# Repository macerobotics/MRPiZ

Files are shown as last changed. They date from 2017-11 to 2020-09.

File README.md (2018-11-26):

# MRPiZ robot

MRPiZ is small Open Source mobile robot.

# Overview

The repository is organised as follows:

* Hardware: schematics of the board
* Software: Python, C, java API and examples
* doc: Documentation

# Generating the documentation

The documentation is made using the [Sphinx tool](http://www.sphinx-dox.org) and the read the doc theme:

    sudo apt install python3-sphinx
    sudo pip3 install sphinx_rtd_theme

To generate the documentation go to the doc/fr directory, then run:

> make html

The output is generated in the build/html dir, open the build/html/index.html
file with firefox.

# Licence

<br />This work is licensed under a <a rel="license" href="http://creativecommons.org/licenses/by-sa/4.0/">Creative Commons Attribution-ShareAlike 4.0 International License</a>.

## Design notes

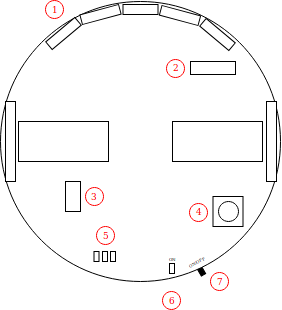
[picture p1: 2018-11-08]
doc/fr/source/overview/overview.png

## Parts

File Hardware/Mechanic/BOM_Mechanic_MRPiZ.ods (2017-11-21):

Description | Quantity | Part Number | Manufacturer
Pololu Ball Caster with 3/8″ Metal Ball | 1 | 951 | Pololu
Pololu Wheel 32×7mm Pair - White | 1 | 1088 | Pololu
Pololu Micro Metal Gearmotor Bracket Extended Pair | 1 | 1089 | Pololu

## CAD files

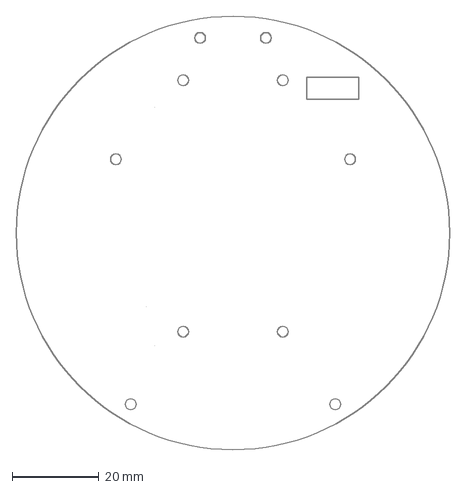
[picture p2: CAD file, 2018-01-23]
Hardware/Mechanic/Dessin_PlaqueMRPiZ.dxf
100.0 x 100.0 mm

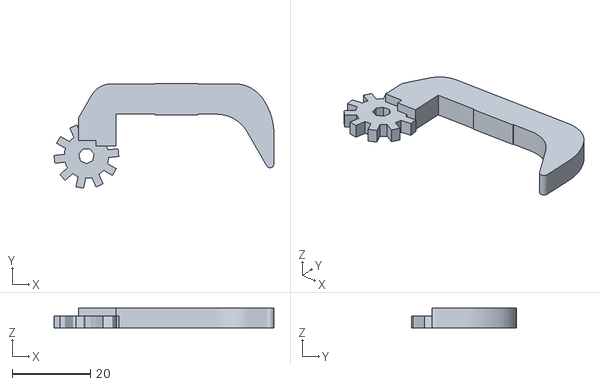
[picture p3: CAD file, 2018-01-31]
Hardware/Mechanic/Gripper/leftpincer.stl
56.3 x 26.8 x 5.00

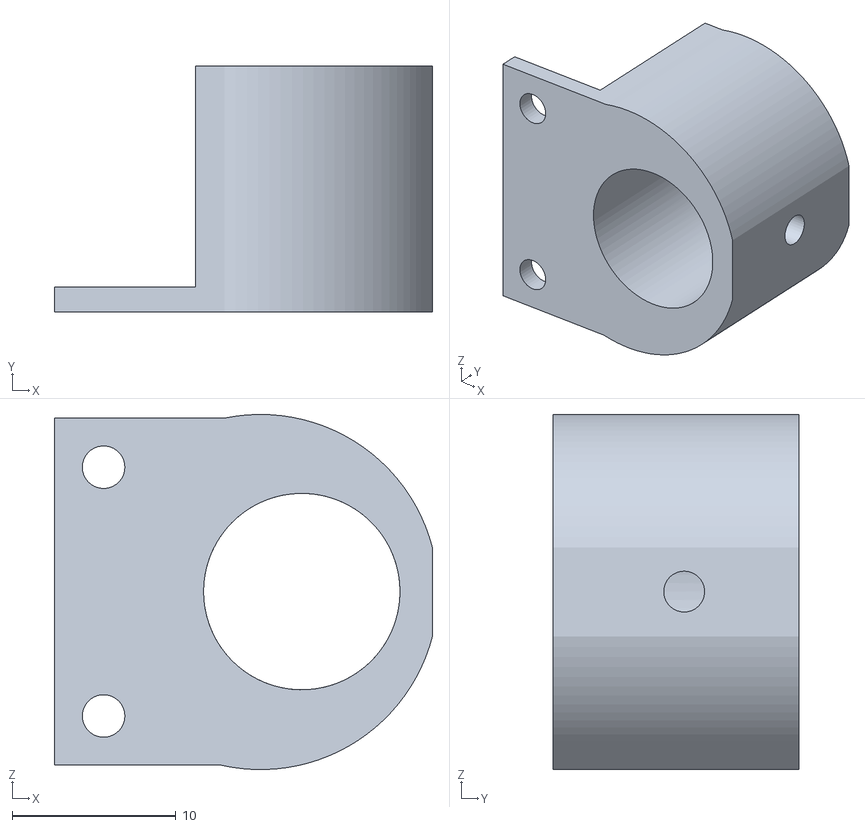
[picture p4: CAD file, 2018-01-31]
Hardware/Mechanic/PencilSupport/PencilSupport.stl
23.1 x 15.0 x 21.7

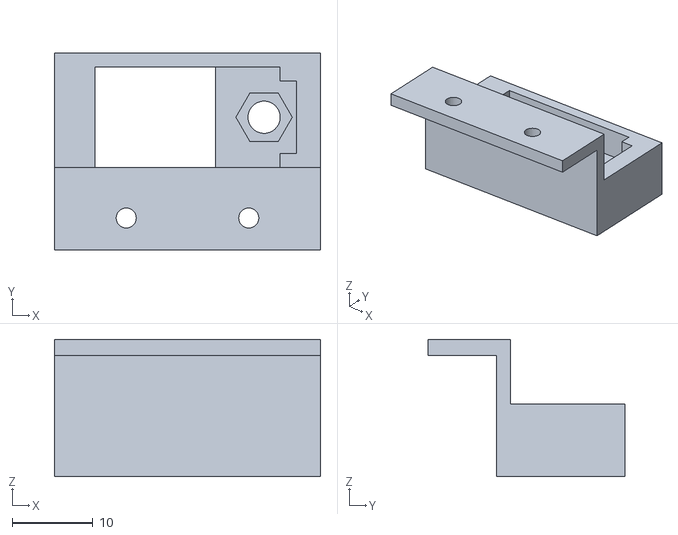
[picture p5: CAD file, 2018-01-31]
Hardware/Mechanic/Gripper/servobox.stl
33.0 x 24.5 x 17.0

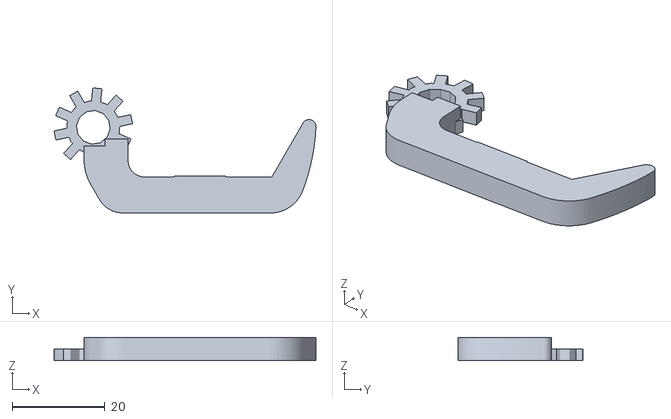
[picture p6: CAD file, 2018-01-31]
Hardware/Mechanic/Gripper/rightpincer.stl
56.5 x 27.0 x 5.00

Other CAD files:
Hardware/Mechanic/Gripper/leftpincer.f3d
Hardware/Mechanic/Gripper/rightpincer.f3d
Hardware/Mechanic/Gripper/servobox.f3d
Hardware/Mechanic/PencilSupport/PencilSupport.f3d

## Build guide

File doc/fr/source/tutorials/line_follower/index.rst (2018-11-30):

Suivi de ligne
==============

Ce tutorial présente l'implémentation d'un suivi de ligne pour le robot MRPiZ.

Matériel nécessaire
-------------------

* Un robot MRPiZ
* Une caméra compatible, idéalement grand angle, ce tutorial
  utilise une [caméra fisheye](https://www.kubii.fr/cameras-accessoires/2292-mini-camera-pour-pi-zero-fisheye-version-kubii-3272496012073.html).

.. warning:: Le connecteur de la raspberry pi zéro n'est pas le mmême que la raspberry pi normale. Il faut donc:

   * soit un adaptateur comme [celui-çi](https://www.kubii.fr/cables-cordons-raspberry-pi/1830-cable-pour-camera-pi-zero-edition-kubii-3272496006768.html),
   * soit une caméra compatible.

Logiciels nécessaire
--------------------

* Python 2.7 (déja installé par défaut),
* La bibliothèque Python MRPiZ (déja installée par défaut),
* OpenCV pour python:

```
$ sudo apt install python-opencv
```

Activation de video4linux
-------------------------

Deux méthodes sont possibles pour accèder à la caméra:

1. PiCamera: la méthode la plus répandue, mais lente car il est nécessaire de transformer l'image pour la mettre au bon format,
2. v4l: qui s'interface directement avec OpenCV, c'est la méthode choisie pour ce tutorial.

Il nous faut donc activer v4l:

.. code:: bash

   $ sudo modprobe bcm2835-v4l2

.. warning::

    Cette commande est a effectuer à chaque redémarrage.

Le suivi de ligne
-----------------

Le fichier complet se trouve dans `Software/Python/tutorials/line_follower/line.py`.

.. warning::

   Utilisez CTRL+C pour arrêter le robot.

Importation des modules
^^^^^^^^^^^^^^^^^^^^^^^

.. code-block:: python

   import numpy as np
   import cv2
   import sys
   from mrpiZ_lib import *

Parametres globaux
^^^^^^^^^^^^^^^^^^

.. code-block:: python

   # image size
   WIDTH = 640
   HEIGHT = 480

   # turn coeff
   COEFF = 0.05
   # base robot speed in straight line
   SPEED = 30

Activation de la caméra
^^^^^^^^^^^^^^^^^^^^^^^

Pour améliorer les performances, la résolution est réduite à 640 pixels en
largeur et 480 en hauteur.

.. code-block:: python

   video_capture = cv2.VideoCapture(0)
   video_capture.set(3, WIDTH)
   video_capture.set(4, HEIGHT)

Boucle principale
^^^^^^^^^^^^^^^^^

La boucle principale va fonctionner à l'infini, pour l'arrêter il faudra
appuyer sur CTRL+C.

.. code-block:: python

   try:
       while(True):

Capture de l'image
^^^^^^^^^^^^^^^^^^

Première étape, on commence par capturer une image.

.. code-block:: python

   # Capture the frames
   ret, frame = video_capture.read()

Voici un exemple d'image capturée:

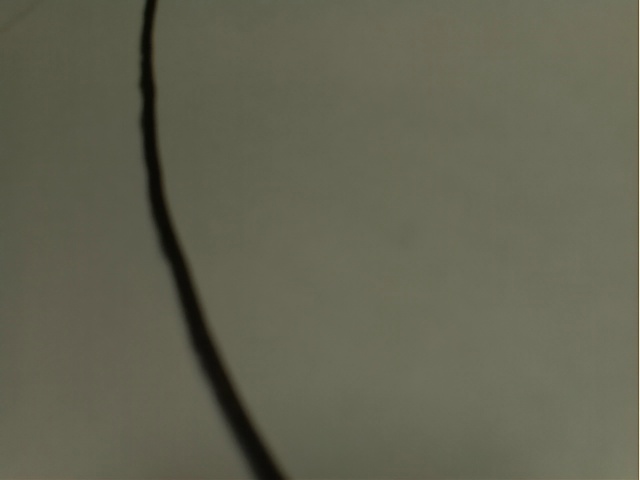
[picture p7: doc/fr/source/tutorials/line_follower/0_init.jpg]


Suppression de la partie haute
^^^^^^^^^^^^^^^^^^^^^^^^^^^^^^

Pour améliorer les performances, on ne va garder que la partie basse de l'image:

.. code-block:: python

   # Crop the image
   # Keep the 100 lower pixels
   crop_img = frame[379:480, 0:640]



Niveaux de gris
^^^^^^^^^^^^^^^

Ensuite on passe l'image en niveaux de gris:

.. code-block:: python

   # Convert to grayscale
   gray = cv2.cvtColor(crop_img, cv2.COLOR_BGR2GRAY)



Flou
^^^^

Un filtre afin de rendre flou les lignes de l'image est appliqué, il permet de
rendre plus efficace les étapes suivantes:

.. code-block:: python

   # Gaussian blur
   blur = cv2.GaussianBlur(gray,(5,5),0)



Seuillage
^^^^^^^^^

Ensuite on va filtrer les parties claires de l'image pour ne garder les parties
noires, pour cela, un filtre de seuillage est appliqué:

.. code-block:: python

   # Color thresholding
   ret,thresh = cv2.threshold(blur,60,255,cv2.THRESH_BINARY_INV)



Détection de contours
^^^^^^^^^^^^^^^^^^^^^

Ensuite, on va utiliser openCV pour détecter les contours:

.. code-block:: python

   # Find the contours of the frame
   contours,hierarchy = cv2.findContours(thresh.copy(), 1, cv2.CHAIN_APPROX_NONE)



Extraction du plus gros contour
^^^^^^^^^^^^^^^^^^^^^^^^^^^^^^^

Il nous faut ensuite extraire la ligne la plus large trouvée afin d'éliminer
les fausses détections:

.. code-block:: python

   # Find the biggest contour (if detected)
   if len(contours) > 0:
       c = max(contours, key=cv2.contourArea)
       M = cv2.moments(c)

       # Skip to avoid div by zero
       if int(M['m00']) == 0:
           continue

Calcul du milieu de la ligne
^^^^^^^^^^^^^^^^^^^^^^^^^^^^

Une fois les contours de la ligne détectée, on calcul le centre de la ligne,
c'est la que l'on veut que le robot aille:

.. code-block:: python

   # Get the line center
   cx = int(M['m10']/M['m00'])
   cy = int(M['m01']/M['m00'])

Contrôle des moteurs
^^^^^^^^^^^^^^^^^^^^

Une correction proportionnelle à la différence entre la position de la ligne et
le milieu de l'image est calculée.  Les moteurs sont ensuite commandés pour
ralentir un des moteurs et accélérer l'autre, ceci afin de faire tourner le
robot en direction du centre de la ligne.

.. code-block:: python

   delta = COEFF * (cx - 320)
   motorRight(0, SPEED - delta)
   motorLeft(0, SPEED + delta)

Clavier
^^^^^^^

Enfin, deux lignes de code permettent d'arrêter le robot quand on appuie sur
CTRL+C.

.. code-block:: python

   except KeyboardInterrupt:
       stop()

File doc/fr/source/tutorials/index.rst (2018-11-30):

=========
Tutorials
=========

.. toctree::
   :maxdepth: 2
   :caption: Contents:

   line_follower/index

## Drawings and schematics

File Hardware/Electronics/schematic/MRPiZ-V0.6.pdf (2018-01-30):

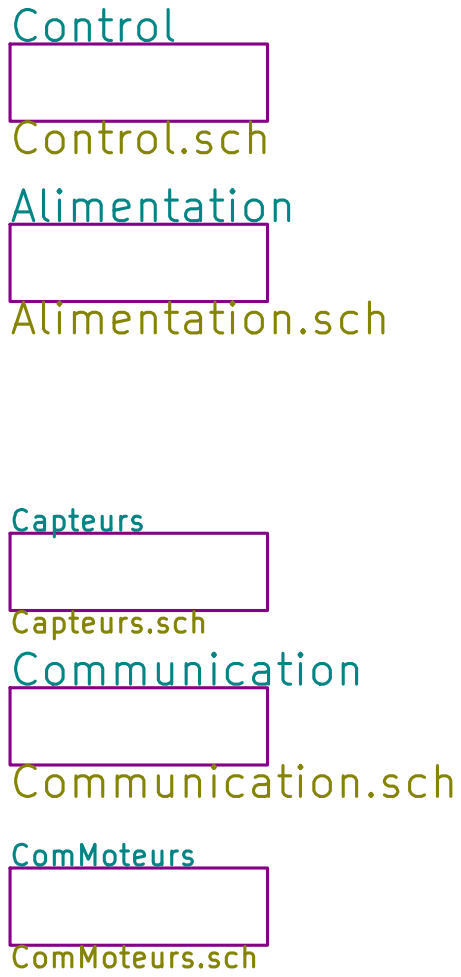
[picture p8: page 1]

ComMoteurs ComMoteurs.sch Control

Control.sch
File: carte_rants_V1.sch Sheet: / Alimentation Alimentation.sch

Capteurs Capteurs.sch Communication

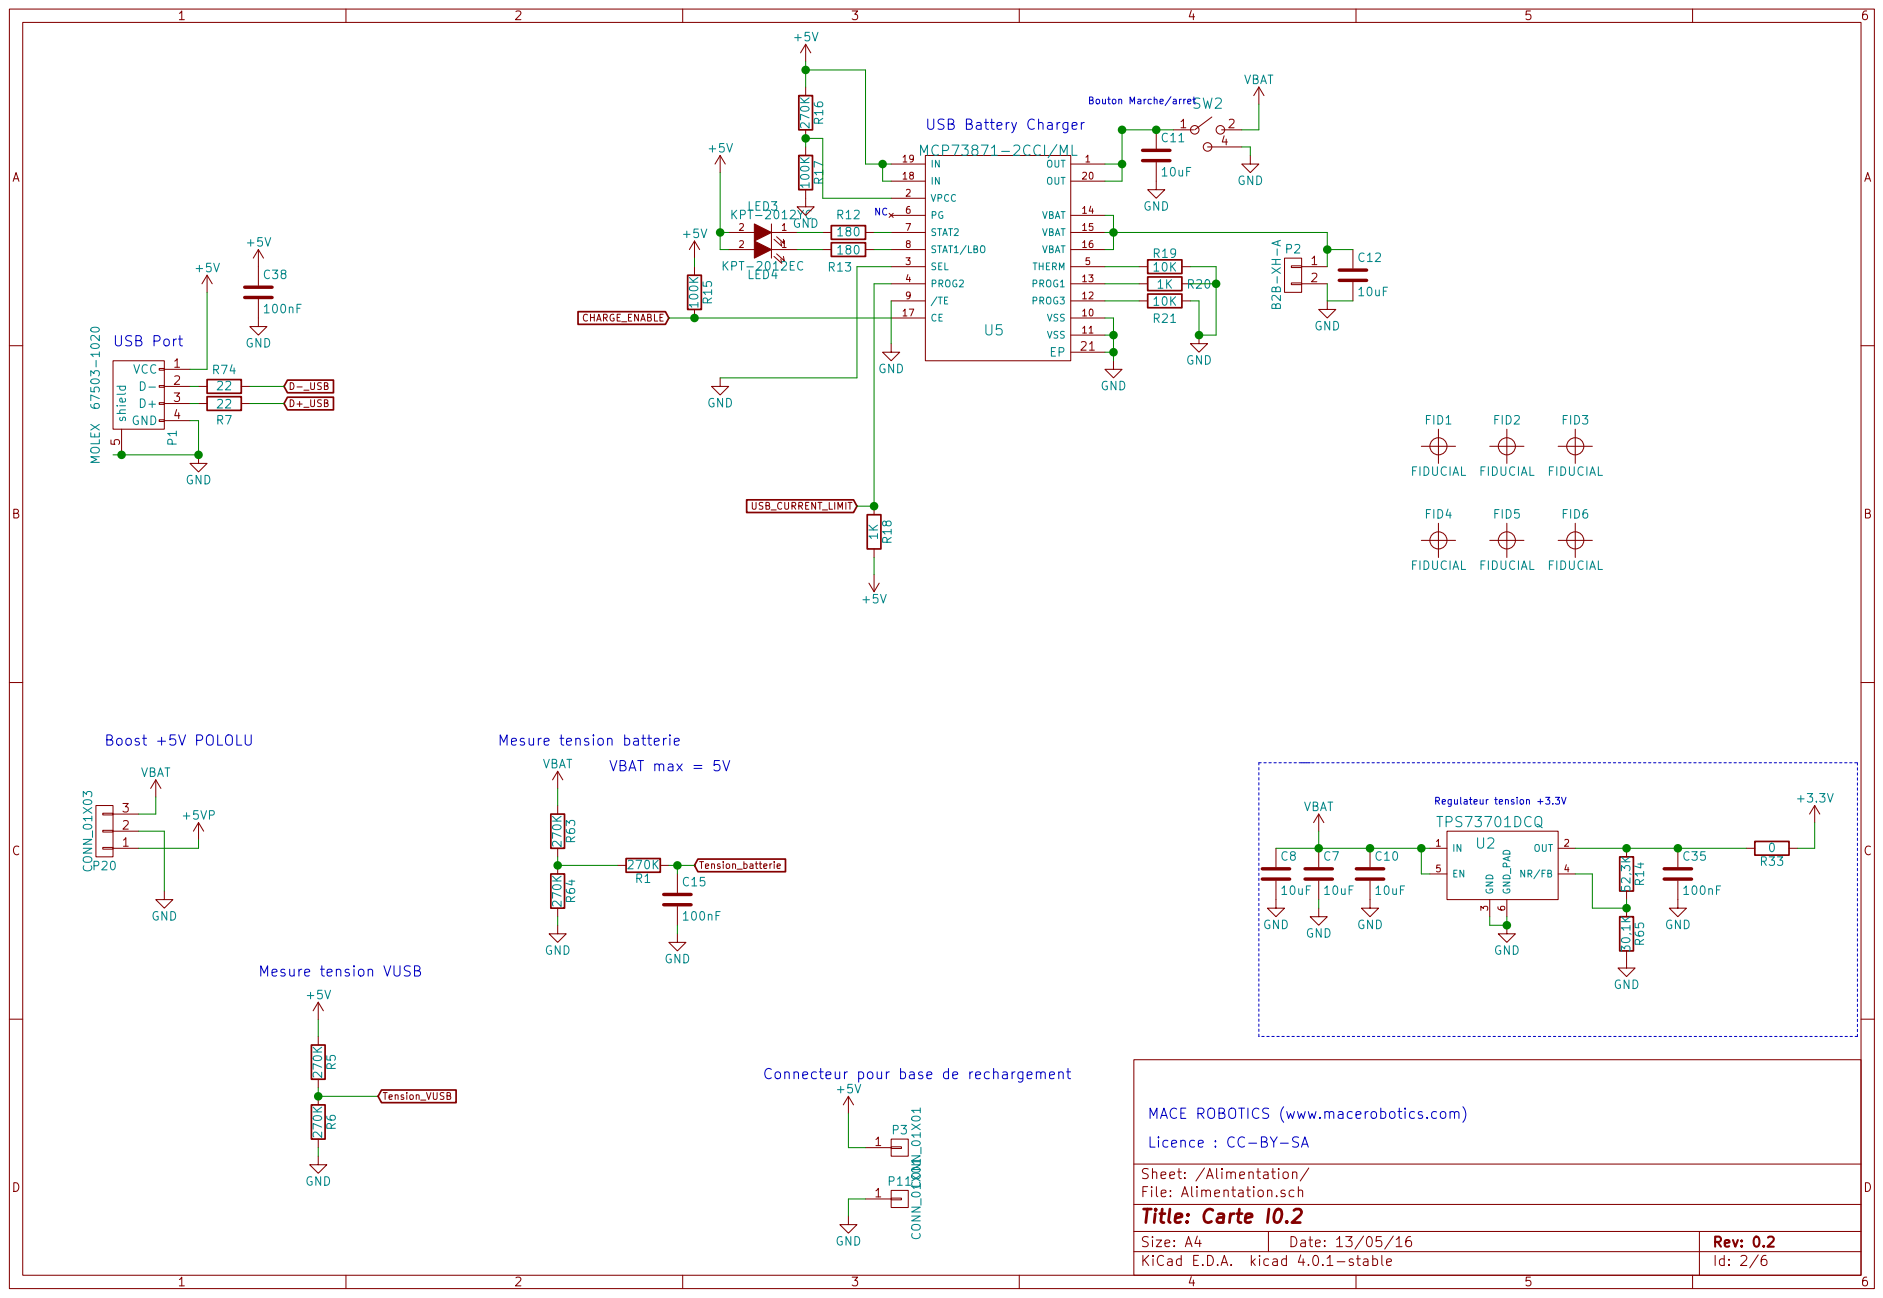
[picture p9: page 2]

VBAT 270K R63 270K R64 Mesure tension batterie GND

1 P11 GND Connecteur pour base de rechargement +5V

Licence : CC-BY-SA

File: Alimentation.sch Sheet: /Alimentation/
Id: 2/6 Title: Carte I0.2

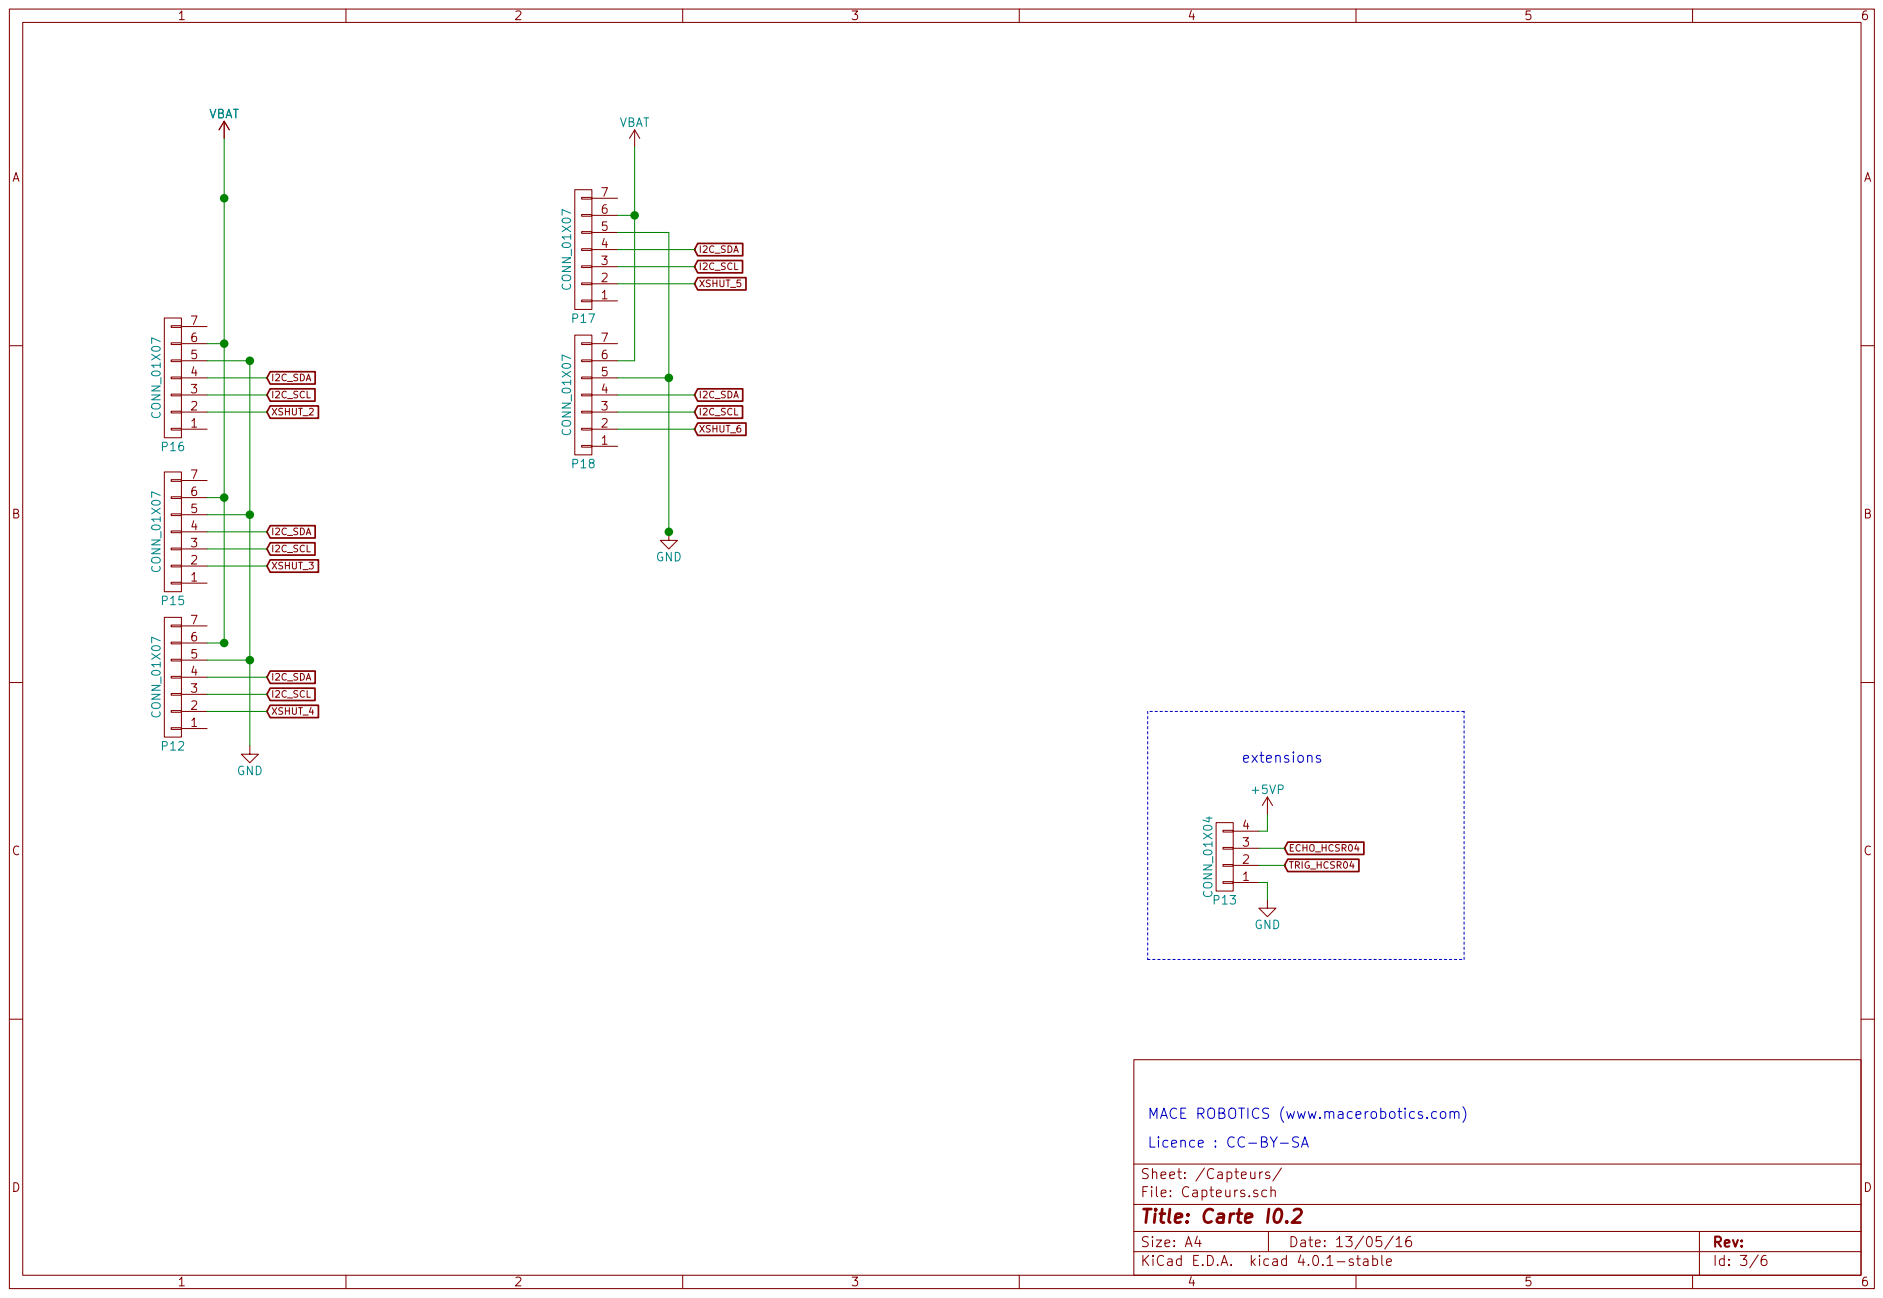
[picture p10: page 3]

MACE ROBOTICS (www.macerobotics.com)

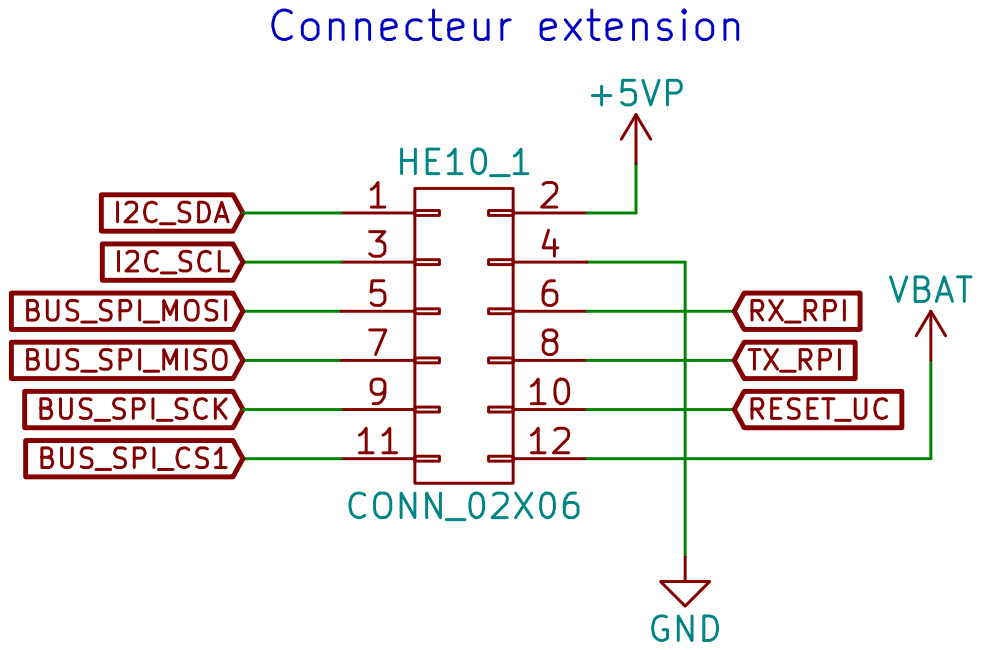
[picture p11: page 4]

Licence : CC-BY-SA

File: Communication.sch Sheet: /Communication/
Id: 4/6 Title: Carte I0.2

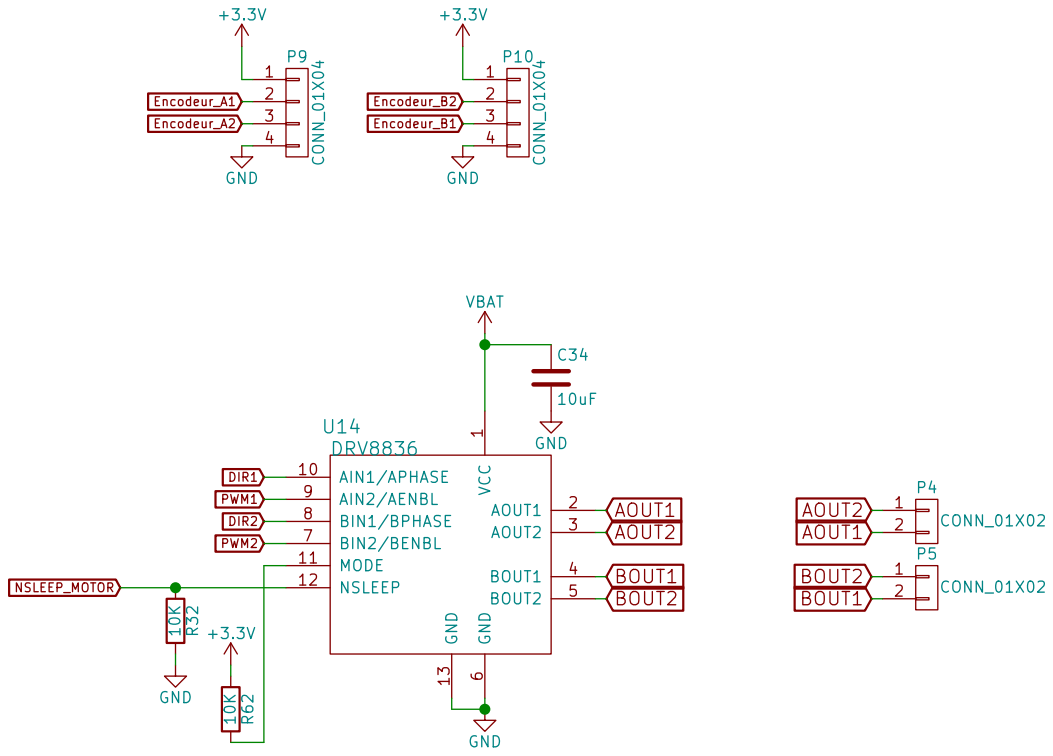
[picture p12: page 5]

4 P9 CONN_01X04 +3.3V
File: ComMoteurs.sch Sheet: /ComMoteurs/ VCC

6 BIN2/BENBL 7 BIN1/BPHASE 8 AIN2/AENBL 9 AIN1/APHASE 10 MODE 11 NSLEEP 12 GND 13 U14 DRV8836 GND

Licence : CC-BY-SA

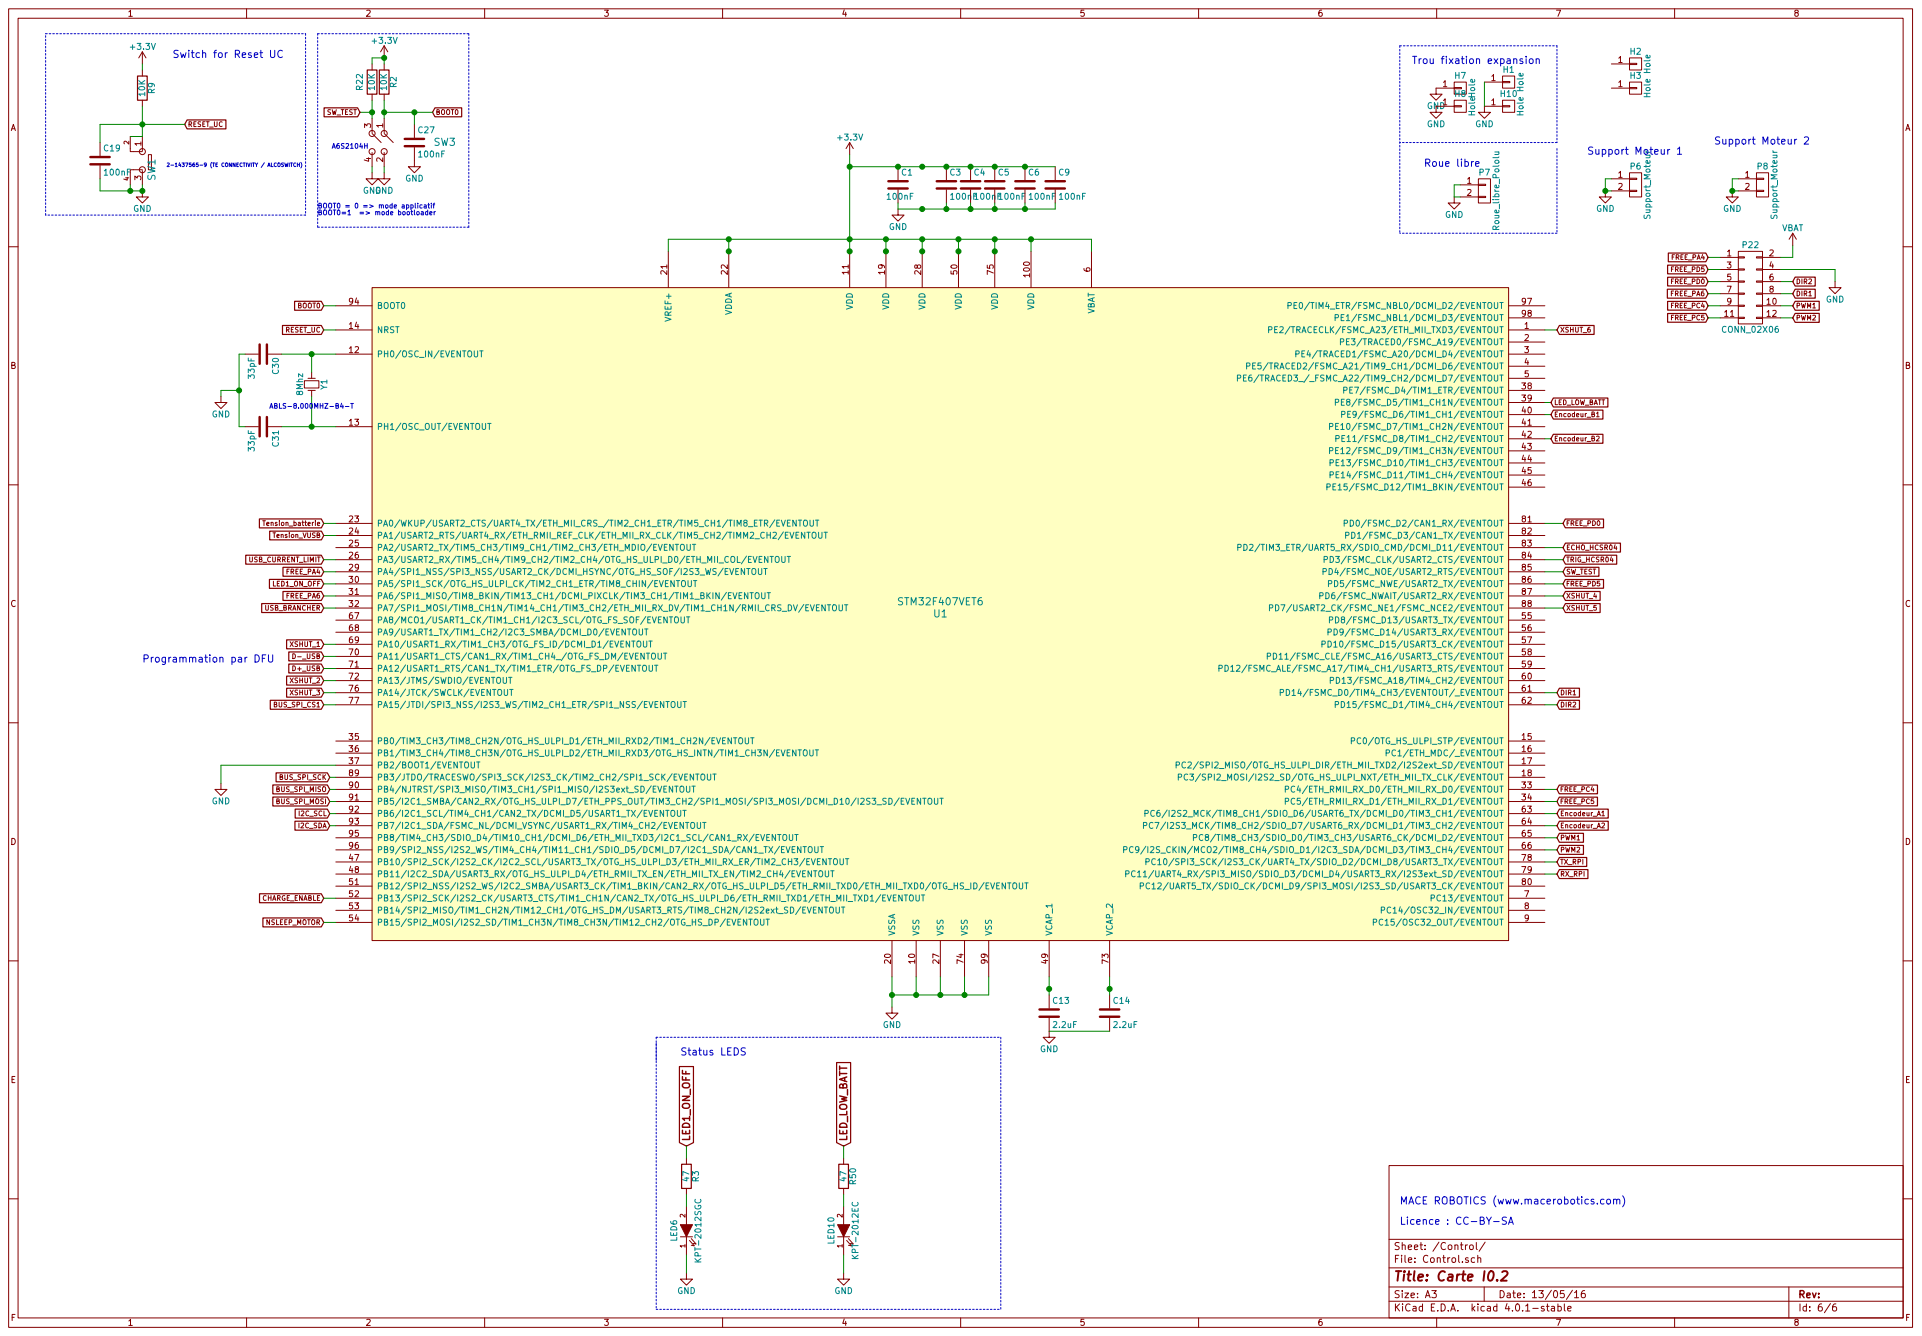
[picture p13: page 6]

BOOT0BOOT0 = 0 => mode applicatif BOOT0=1 => mode bootloader R2 10K
RESET_UC GND

2-1437565-9 (TE CONNECTIVITY / ALCOSWITCH) Switch for Reset UC

LED_LOW_BATT MACE ROBOTICS (www.macerobotics.com)

6 PC13/EVENTOUT 7 PC14/OSC32_IN/EVENTOUT 8 PC15/OSC32_OUT/EVENTOUT 9 VSS 10 VSSA 20

File: Control.sch Sheet: /Control/ GND

Licence : CC-BY-SA

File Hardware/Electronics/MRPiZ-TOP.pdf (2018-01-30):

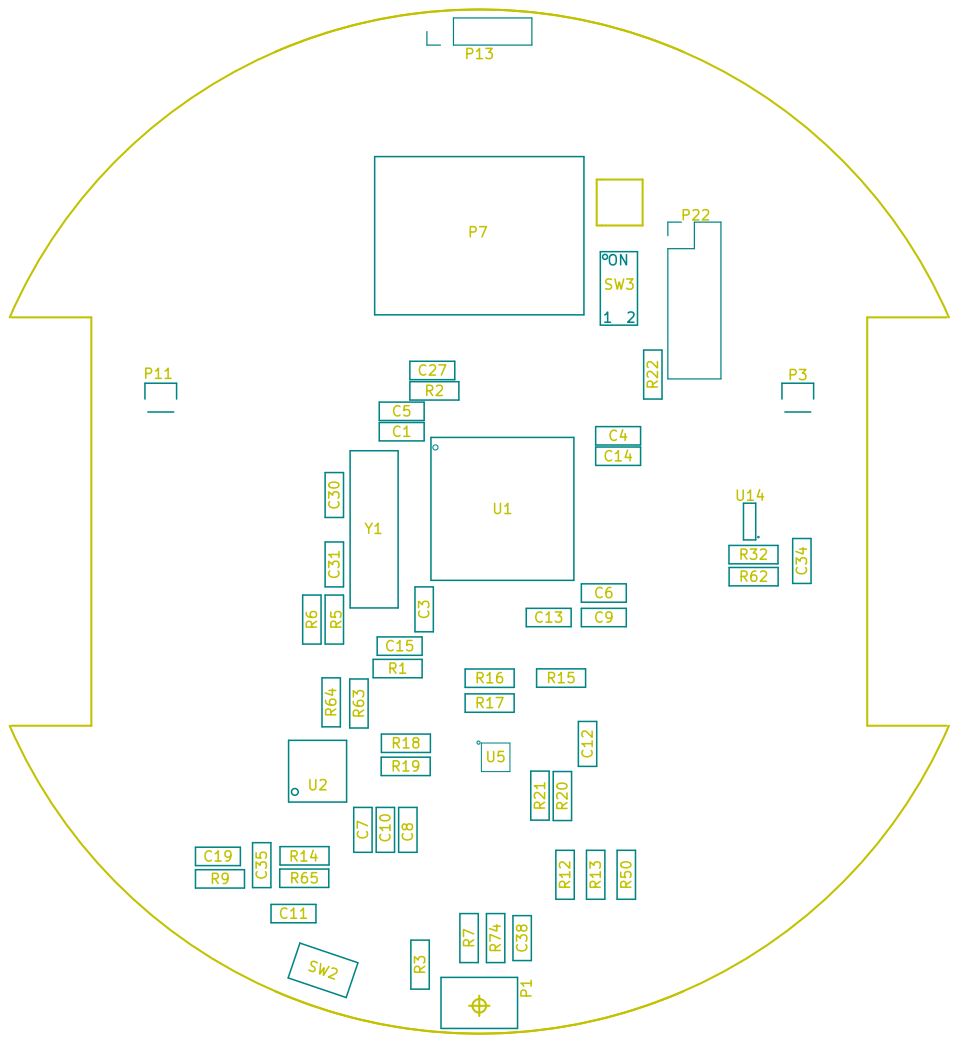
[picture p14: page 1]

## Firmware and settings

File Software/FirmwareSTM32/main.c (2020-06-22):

/**
  ******************************************************************************
  * @file    main.c
  * @author  Ac6
  * @version V1.0
  * @date    12/06/20
  * @brief   main function.
  ******************************************************************************
*/


#include "stm32f4xx.h"
#include "board.h"


/* Private function prototypes -----------------------------------------------*/
void SystemClock_Config(void);

int main(void)
{

  /* Reset of all peripherals, Initializes the Flash interface and the Systick. */
  HAL_Init();

  /* Configure the system clock */
  SystemClock_Config();

  // init delay functions
  Delay_init();

  // init scheduler
  schedulerInit();

  Board_init();

  // init serial communication between RPi and STM32
  ComRPI_init();

  RobotState_init();

  Motors_init();

  // init magnetic encoder
  encoder_init();

  Usart_Send_String(UART4, "START ROBOT MRPiZ");

  positionControl_init();

  ProxSensorsVL6180_init();


  while(1)
  {

	  schedulerManage();

  }// end while
}


/**
  * @brief System Clock Configuration
  * @retval None
  */
void SystemClock_Config(void)
{
  RCC_OscInitTypeDef RCC_OscInitStruct = {0};
  RCC_ClkInitTypeDef RCC_ClkInitStruct = {0};

  /** Configure the main internal regulator output voltage
  */
  __HAL_RCC_PWR_CLK_ENABLE();
  __HAL_PWR_VOLTAGESCALING_CONFIG(PWR_REGULATOR_VOLTAGE_SCALE1);
  /** Initializes the CPU, AHB and APB busses clocks
  */
  RCC_OscInitStruct.OscillatorType = RCC_OSCILLATORTYPE_HSI;
  RCC_OscInitStruct.HSIState = RCC_HSI_ON;
  RCC_OscInitStruct.HSICalibrationValue = RCC_HSICALIBRATION_DEFAULT;
  RCC_OscInitStruct.PLL.PLLState = RCC_PLL_ON;
  RCC_OscInitStruct.PLL.PLLSource = RCC_PLLSOURCE_HSI;
  RCC_OscInitStruct.PLL.PLLM = 8;
  RCC_OscInitStruct.PLL.PLLN = 168;
  RCC_OscInitStruct.PLL.PLLP = RCC_PLLP_DIV2;
  RCC_OscInitStruct.PLL.PLLQ = 4;
  if (HAL_RCC_OscConfig(&RCC_OscInitStruct) != HAL_OK)
  {
    //Error_Handler();
  }
  /** Initializes the CPU, AHB and APB busses clocks
  */
  RCC_ClkInitStruct.ClockType = RCC_CLOCKTYPE_HCLK|RCC_CLOCKTYPE_SYSCLK
                              |RCC_CLOCKTYPE_PCLK1|RCC_CLOCKTYPE_PCLK2;
  RCC_ClkInitStruct.SYSCLKSource = RCC_SYSCLKSOURCE_PLLCLK;
  RCC_ClkInitStruct.AHBCLKDivider = RCC_SYSCLK_DIV1;
  RCC_ClkInitStruct.APB1CLKDivider = RCC_HCLK_DIV4;
  RCC_ClkInitStruct.APB2CLKDivider = RCC_HCLK_DIV2;

  if (HAL_RCC_ClockConfig(&RCC_ClkInitStruct, FLASH_LATENCY_5) != HAL_OK)
  {
    //Error_Handler();
  }
}

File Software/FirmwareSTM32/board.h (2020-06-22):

/**
  ******************************************************************************
  * @file    Board.h
  * @author  Mace Robotics
  * @version V1.0
  * @date    12/06/2020
  * @brief	 Definition of the I/O
  *
 *******************************************************************************/
#ifndef _BOARD_H
#define _BOARD_H


#include <math.h>
#include <stdbool.h>
#include "stm32f4xx.h"
#include "leds.h"
#include "batteryTension.h"
#include "encoder.h"
#include "motors.h"
#include "firmwareVersion.h"
#include "ledOnOff.h"
#include "proximitySensors.h"
#include "trapezoidGenerator.h"
#include "robotState.h"
#include "scheduler.h"
#include "moveRobot.h"
#include "positionControl.h"
#include "delay.h"
#include "vl6180x.h"
#include "i2c.h"
#include "adc.h"
#include "switchs.h"
#include "chargeManagement.h"
#include "usart.h"
#include "comRPI.h"
#include "control.h"

/**
  * @brief LEDS
  */
#define LED1_PORT GPIOA // LED ON/OFF
#define LED1_PIN  GPIO_PIN_5

#define LED2_PORT GPIOE       // LOW BATTERY
#define LED2_PIN  GPIO_PIN_8



/**
  * @brief Proximity XSHUT
  */
#define PROX1_XSHUT_PORT GPIOA
#define PROX1_XSHUT_PIN  GPIO_PIN_13

#define PROX2_XSHUT_PORT GPIOA
#define PROX2_XSHUT_PIN  GPIO_PIN_14

#define PROX3_XSHUT_PORT GPIOD
#define PROX3_XSHUT_PIN  GPIO_PIN_6

#define PROX4_XSHUT_PORT GPIOD
#define PROX4_XSHUT_PIN  GPIO_PIN_7

#define PROX5_XSHUT_PORT GPIOE
#define PROX5_XSHUT_PIN  GPIO_PIN_2



/**
  * @brief I2C BUS
  */
#define I2C_SDA_PORT GPIOB
#define I2C_SDA_PIN  GPIO_PIN_7

#define I2C_SCL_PORT GPIOB
#define I2C_SCL_PIN  GPIO_PIN_6

/**
  * @brief SPI BUS
  */
#define SPI_SCK_PORT GPIOB
#define SPI_SCK_PIN  GPIO_PIN_3

#define SPI_MISO_PORT GPIOB
#define SPI_MISO_PIN  GPIO_PIN_4

#define SPI_MOSI_PORT GPIOB
#define SPI_MOSI_PIN  GPIO_PIN_5

#define SPI_CS1_PORT GPIOA
#define SPI_CS1_PIN  GPIO_PIN_15


/**
  * @brief Battery Tension
  */
#define BATT_PORT GPIOA
#define BATT_PIN  GPIO_PIN_0

/**
  * @brief H-Bridge DC Motor
  */
#define HBRIDGE_DIR1_PORT GPIOD
#define HBRIDGE_DIR1_PIN  GPIO_PIN_14

#define HBRIDGE_DIR2_PORT GPIOD
#define HBRIDGE_DIR2_PIN  GPIO_PIN_15

#define HBRIDGE_PWM1_PORT GPIOC
#define HBRIDGE_PWM1_PIN  GPIO_PIN_8

#define HBRIDGE_PWM2_PORT GPIOC
#define HBRIDGE_PWM2_PIN  GPIO_PIN_9

#define HBRIDGE_SLEEP_PORT GPIOB
#define HBRIDGE_SLEEP_PIN  GPIO_PIN_15

/**
  * @brief USB  management
  */
#define USB_CURRENT_PORT GPIOA
#define USB_CURRENT_PIN  GPIO_PIN_3

#define USB_PRESENT_PORT GPIOA
#define USB_PRESENT_PIN  GPIO_PIN_7

#define USB_VOLTAGE_PORT GPIOA
#define USB_VOLTAGE_PIN  GPIO_PIN_1


/**
  * @brief Switchs
  */
#define SWITCH1_PORT GPIOD
#define SWITCH1_PIN  GPIO_PIN_4



/**
  * @brief Encoder
  */
#define ENCOD1A_PORT GPIOC
#define ENCOD1A_PIN  GPIO_PIN_6

#define ENCOD1B_PORT GPIOC
#define ENCOD1B_PIN  GPIO_PIN_7

#define ENCOD2A_PORT GPIOE
#define ENCOD2A_PIN  GPIO_PIN_9

#define ENCOD2B_PORT GPIOE
#define ENCOD2B_PIN  GPIO_PIN_11


void Board_init(void);

#endif
// End Of File

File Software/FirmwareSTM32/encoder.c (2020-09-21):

/**
  ******************************************************************************
  * @file    Encoder.c
  * @author  Mace Robotics
  * @version V1.1
  * @date    21/09/2020
  * @brief
  *
  * Modification du 21/09/20 : ajouter TIM_AUTORELOAD_PRELOAD_DISABLE;
  *
  *
 *******************************************************************************/
#include <stdbool.h>
#include "encoder.h"

typedef struct
{
int32_t currentTimer;
int32_t direction;
int32_t oldTimer;
int32_t virtualTimer;
TIM_TypeDef* TIMER;
bool OverFlow;
}struct_Encoder;



static void encoder_iniTimer1(void);
static void encoder_iniTimer8(void);
static int32_t EncoderVirtual(struct_Encoder *Encoder);




struct_Encoder EncoderRight, EncoderLeft;


/**********************************************************
 * @brief  Encoder initialisation
 * @param  None
 * @retval None
**********************************************************/
void encoder_init(void)
{
GPIO_InitTypeDef gpio_initStruct;


  /* Configuration  gpio  encoder 1 */
  gpio_initStruct.Pin = ENCOD1A_PIN | ENCOD1B_PIN; // Pin
  gpio_initStruct.Mode = GPIO_MODE_AF_PP;
  gpio_initStruct.Speed = GPIO_SPEED_HIGH;
  gpio_initStruct.Pull = GPIO_PULLUP;
  gpio_initStruct.Alternate = GPIO_AF3_TIM8;
  HAL_GPIO_Init(ENCOD1A_PORT, &gpio_initStruct);

  /* Configuration  gpio  encoder 2 */
  gpio_initStruct.Pin = ENCOD2A_PIN | ENCOD2B_PIN; // Pin
  gpio_initStruct.Mode = GPIO_MODE_AF_PP;
  gpio_initStruct.Speed = GPIO_SPEED_HIGH;
  gpio_initStruct.Pull = GPIO_PULLUP;
  gpio_initStruct.Alternate = GPIO_AF1_TIM1;
  HAL_GPIO_Init(ENCOD2A_PORT, &gpio_initStruct);

  // Init timer 1
  encoder_iniTimer1();

  // Init timer 8
  encoder_iniTimer8();

  // Init virtual encoder right
  EncoderRight.TIMER = TIM1;
  EncoderRight.OverFlow = false;
  EncoderRight.direction = 0;
  EncoderRight.currentTimer = 0;
  EncoderRight.oldTimer = 0;

  // Init virtual encoder right
  EncoderLeft.TIMER = TIM8;
  EncoderLeft.OverFlow = false;
  EncoderLeft.direction = 0;
  EncoderLeft.currentTimer = 0;
  EncoderLeft.oldTimer = 0;

  // Clear the flag de l'overflow
  (EncoderRight.TIMER)->SR = (EncoderRight.TIMER)->SR & 0xFFFE;
  // Clear the flag de l'overflow
  (EncoderLeft.TIMER)->SR = (EncoderLeft.TIMER)->SR & 0xFFFE;



}




/**********************************************************
 * @brief  read encoder left
 * @param  None
 * @retval None
**********************************************************/
int32_t encodeurLeft(void)
{
int32_t counter = 0;

  EncoderLeft.currentTimer = TIM1->CNT;

  counter = EncoderVirtual(&EncoderLeft);

  return(counter);
}

/**********************************************************
 * @brief  read encoder right
 * @param  None
 * @retval None
**********************************************************/
int32_t encodeurRight(void)
{
int32_t counter = 0;

  // read the counter timer.
  EncoderRight.currentTimer = TIM8->CNT;

  counter = EncoderVirtual(&EncoderRight);

  return(counter);

}


/**********************************************************
 * @brief  encodeur Right reset
 * @param  None
 * @retval None
**********************************************************/
void encodeur_reset(void)
{
  EncoderRight.virtualTimer = 0;
  EncoderLeft.virtualTimer = 0;
  TIM8->CNT = 0;
  TIM1->CNT = 0;
}


/**********************************************************
 * @brief  virtual 32 bit encoder
 * @param  None
 * @retval None
**********************************************************/
static int32_t EncoderVirtual(struct_Encoder *Encoder)
{
int16_t Difference = 0;

  // Calcul de la différence par rapport à l'ancienne valeur.
  if(Encoder->oldTimer < Encoder->currentTimer)
  {
    Difference = Encoder->currentTimer - Encoder->oldTimer;
  }
  else
  {
    Difference = (65536 - Encoder->oldTimer) + Encoder->currentTimer;
  }

  Encoder->virtualTimer = Encoder->virtualTimer + Difference;

  Encoder->oldTimer = Encoder->virtualTimer;

  //return(-Encoder->virtualTimer);
  return(-Encoder->virtualTimer/7); // pour moteur avec encodeur de 2800

}


/**********************************************************
 * @brief  Encoder init timer 1
 * @param  None
 * @retval None
**********************************************************/
static void encoder_iniTimer1(void)
{
TIM_HandleTypeDef timer1_initStruct;
TIM_Encoder_InitTypeDef t1Encod_initStruct;

  // TIM1 Clock Enable
  __TIM1_CLK_ENABLE();

  // Timer 1 init structure
  timer1_initStruct.Instance = TIM1;
  timer1_initStruct.Init.Prescaler = 0;
  timer1_initStruct.Init.CounterMode = TIM_COUNTERMODE_UP;
  timer1_initStruct.Init.Period = 0xFFFF;
  timer1_initStruct.Init.ClockDivision = TIM_CLOCKDIVISION_DIV1;
  timer1_initStruct.Init.AutoReloadPreload = TIM_AUTORELOAD_PRELOAD_DISABLE;

  t1Encod_initStruct.EncoderMode = TIM_ENCODERMODE_TI12;

  t1Encod_initStruct.IC1Polarity = TIM_INPUTCHANNELPOLARITY_RISING;
  t1Encod_initStruct.IC2Polarity = TIM_INPUTCHANNELPOLARITY_RISING;

  t1Encod_initStruct.IC1Selection = TIM_ICSELECTION_DIRECTTI;
  t1Encod_initStruct.IC2Selection = TIM_ICSELECTION_DIRECTTI;

  t1Encod_initStruct.IC1Prescaler = TIM_ICPSC_DIV1;
  t1Encod_initStruct.IC2Prescaler = TIM_ICPSC_DIV1;

   t1Encod_initStruct.IC1Filter = 8;// digital filter
   t1Encod_initStruct.IC2Filter = 8;// digital filter

  // Init timer
  HAL_TIM_Encoder_Init(&timer1_initStruct,&t1Encod_initStruct);

  __HAL_TIM_SetCounter(&timer1_initStruct,0);

  HAL_TIM_Encoder_Start(&timer1_initStruct, TIM_CHANNEL_1 | TIM_CHANNEL_2);

}

/**********************************************************
 * @brief  Encoder init timer 8
 * @param  None
 * @retval None
**********************************************************/
static void encoder_iniTimer8(void)
{
TIM_HandleTypeDef timer8_initStruct;
TIM_Encoder_InitTypeDef t8Encod_initStruct;

  // TIM8 Clock Enable
  __TIM8_CLK_ENABLE();

  // Timer 8 init structure
  timer8_initStruct.Instance = TIM8;
  timer8_initStruct.Init.Prescaler = 0;
  timer8_initStruct.Init.CounterMode = TIM_COUNTERMODE_UP;
  timer8_initStruct.Init.Period = 0xFFFF;
  timer8_initStruct.Init.ClockDivision = TIM_CLOCKDIVISION_DIV1;
  timer8_initStruct.Init.AutoReloadPreload = TIM_AUTORELOAD_PRELOAD_DISABLE;

  t8Encod_initStruct.EncoderMode = TIM_ENCODERMODE_TI12;

  t8Encod_initStruct.IC1Polarity = TIM_INPUTCHANNELPOLARITY_RISING;
  t8Encod_initStruct.IC2Polarity = TIM_INPUTCHANNELPOLARITY_RISING;

  t8Encod_initStruct.IC1Selection = TIM_ICSELECTION_DIRECTTI;
  t8Encod_initStruct.IC2Selection = TIM_ICSELECTION_DIRECTTI;

  t8Encod_initStruct.IC1Prescaler = TIM_ICPSC_DIV1;
  t8Encod_initStruct.IC2Prescaler = TIM_ICPSC_DIV1;

  t8Encod_initStruct.IC1Filter = 8;// digital filter
  t8Encod_initStruct.IC2Filter = 8;// digital filter


  // Init timer
  HAL_TIM_Encoder_Init(&timer8_initStruct,&t8Encod_initStruct);

  __HAL_TIM_SetCounter(&timer8_initStruct,0);

  HAL_TIM_Encoder_Start(&timer8_initStruct, TIM_CHANNEL_1 | TIM_CHANNEL_2);

}


 // End Of file

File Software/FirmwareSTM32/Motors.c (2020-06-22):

/**
  ******************************************************************************
  * @file    main.c
  * @author  Ac6
  * @version V1.0
  * @date    12/06/20
  * @brief   motors
  ******************************************************************************
*/


#include <motors.h>
#include "stm32f4xx.h"

struct_motor s_motorRight;
struct_motor s_motorLeft;



TIM_HandleTypeDef TIMER_InitStruct;
TIM_OC_InitTypeDef TIMER_OC_InitStruct;


/**********************************************************
 * @brief  Motors_init : motor initialisation
 * @param
 * @retval None
**********************************************************/
void Motors_init(void)
{
GPIO_InitTypeDef GPIO_DIR_InitStruct;
GPIO_InitTypeDef GPIO_PWM_InitStruct;

  /* GPIO Ports Clock Enable */
  __GPIOC_CLK_ENABLE();
  __GPIOD_CLK_ENABLE();

  /* GPIOD Configuration: Direction */
  GPIO_DIR_InitStruct.Pin = HBRIDGE_DIR1_PIN | HBRIDGE_DIR2_PIN; // Pin direction
  GPIO_DIR_InitStruct.Mode = GPIO_MODE_OUTPUT_PP;
  GPIO_DIR_InitStruct.Pull = GPIO_NOPULL;
  HAL_GPIO_Init(GPIOD, &GPIO_DIR_InitStruct);

  /* GPIOE Configuration: sleep pin */
  GPIO_DIR_InitStruct.Pin = HBRIDGE_SLEEP_PIN; // Pin direction
  GPIO_DIR_InitStruct.Mode = GPIO_MODE_OUTPUT_PP;
  GPIO_DIR_InitStruct.Pull = GPIO_NOPULL;
  HAL_GPIO_Init(HBRIDGE_SLEEP_PORT, &GPIO_DIR_InitStruct);

  /* GPIOC PWM Configuration: TIM3 CH3 (PC8) and TIM3 CH4 (PC9) */
  GPIO_PWM_InitStruct.Pin = HBRIDGE_PWM1_PIN | HBRIDGE_PWM2_PIN ;
  GPIO_PWM_InitStruct.Mode = GPIO_MODE_AF_PP;
  GPIO_PWM_InitStruct.Speed = GPIO_SPEED_HIGH;
  GPIO_PWM_InitStruct.Alternate = GPIO_AF2_TIM3;
  HAL_GPIO_Init(GPIOC, &GPIO_PWM_InitStruct);

    /* TIM3 Clock Enable */
  __TIM3_CLK_ENABLE();


  /* TIM3 is connected to APB1 bus : so 42MHz  clock. But PLL double this frequency => 42*2 = 84 Mhz    */
  /* Timer_Frequency = (84Mhz) / (Prescaler +1 )                                                                                                */
  /*  TIMER_Period = (Timer_Frequency) / (PWM_frequency) - 1                                                                    */

  // Init TIMER3 for 20 Khz frequency (PWM motors)
  TIMER_InitStruct.Instance = TIM3;
  TIMER_InitStruct.Init.Prescaler = 0; // Timer_Frequency = 84 Mhz.
  TIMER_InitStruct.Init.CounterMode = TIM_COUNTERMODE_UP;
  TIMER_InitStruct.Init.Period = 4199; //  TIMER_Period = (84M)/(20k) - 1 = 4199


  TIMER_InitStruct.Init.ClockDivision = TIM_CLOCKDIVISION_DIV1;
  HAL_TIM_PWM_Init(&TIMER_InitStruct);

  // Output Compare Configuration
  TIMER_OC_InitStruct.OCMode = TIM_OCMODE_PWM1;
  TIMER_OC_InitStruct.OCIdleState = TIM_OCIDLESTATE_SET;
  TIMER_OC_InitStruct.Pulse = 0;// PWM 0 %
  TIMER_OC_InitStruct.OCPolarity = TIM_OCPOLARITY_HIGH;
  TIMER_OC_InitStruct.OCFastMode = TIM_OCFAST_ENABLE;



  HAL_TIM_PWM_ConfigChannel(&TIMER_InitStruct, &TIMER_OC_InitStruct, TIM_CHANNEL_3);
  HAL_TIM_PWM_ConfigChannel(&TIMER_InitStruct, &TIMER_OC_InitStruct, TIM_CHANNEL_4);

  HAL_TIM_PWM_Start(&TIMER_InitStruct,TIM_CHANNEL_3);
  HAL_TIM_PWM_Start(&TIMER_InitStruct,TIM_CHANNEL_4);

  // Enable nsleep
  HAL_GPIO_WritePin(HBRIDGE_SLEEP_PORT, HBRIDGE_SLEEP_PIN, GPIO_PIN_SET);

  s_motorRight.speed = 0;
  s_motorLeft.speed = 0;
  s_motorRight.direction = MOTOR_FORWARD;
  s_motorLeft.direction = MOTOR_FORWARD;

}


/**********************************************************
 * @brief  Motor_right
 * @param  Direction and speed of the motor (0 to 100)
 * @retval None
**********************************************************/
void Motor_right(MotorDir_TypeDef Motor_Direction, uint32_t Motor_Speed)
{
	  s_motorRight.speed = Motor_Speed;
	  s_motorRight.direction = Motor_Direction;

	  // Direction
	  if( Motor_Direction == MOTOR_FORWARD )
	  {
		// State low
		HAL_GPIO_WritePin(HBRIDGE_DIR1_PORT, HBRIDGE_DIR1_PIN, GPIO_PIN_RESET);
	  }
	  else
	  {
		// State high
	    HAL_GPIO_WritePin(HBRIDGE_DIR1_PORT, HBRIDGE_DIR1_PIN, GPIO_PIN_SET);
	  }

	  TIMER_OC_InitStruct.Pulse = (Motor_Speed*TIMER_InitStruct.Init.Period)/100;
	  HAL_TIM_PWM_ConfigChannel(&TIMER_InitStruct, &TIMER_OC_InitStruct, TIM_CHANNEL_3);

	  HAL_TIM_PWM_Start(&TIMER_InitStruct,TIM_CHANNEL_3);


}


/**********************************************************
 * @brief  Motor_left
 * @param  Direction and speed of the motor (0 to 100)
 * @retval None
**********************************************************/
void Motor_left(MotorDir_TypeDef Motor_Direction, uint32_t Motor_Speed)
{
	  s_motorLeft.speed = Motor_Speed;
	  s_motorLeft.direction = Motor_Direction;

	  if( Motor_Direction == MOTOR_FORWARD )
	  {
		// State low
		HAL_GPIO_WritePin(HBRIDGE_DIR2_PORT, HBRIDGE_DIR2_PIN, GPIO_PIN_RESET);
	  }
	  else
	  {
		// State high
	    HAL_GPIO_WritePin(HBRIDGE_DIR2_PORT, HBRIDGE_DIR2_PIN, GPIO_PIN_SET);
	  }


	  TIMER_OC_InitStruct.Pulse = (Motor_Speed*TIMER_InitStruct.Init.Period)/100;
	  HAL_TIM_PWM_ConfigChannel(&TIMER_InitStruct, &TIMER_OC_InitStruct, TIM_CHANNEL_4);

	  HAL_TIM_PWM_Start(&TIMER_InitStruct,TIM_CHANNEL_4);

}


/**********************************************************
 * @brief  Motors_write
 * @param  Direction and speed of the motor (0 to 100)
 * @retval None
**********************************************************/
void Motors_write(MotorDir_TypeDef Motor_DirectionRight,
		          MotorDir_TypeDef Motor_DirectionLeft,
		          uint32_t Motor_SpeedRight,
		          uint32_t Motor_SpeedLeft)
{

  Motor_right(Motor_DirectionRight, Motor_SpeedRight);
  Motor_left(Motor_DirectionLeft, Motor_SpeedLeft);

}


/**********************************************************
 * @brief  Motors_stop
 * @param  Direction and speed of the motor (0 to 100)
 * @retval None
**********************************************************/
void Motors_stop(void)
{
	  TIMER_OC_InitStruct.Pulse = 0;
	  HAL_TIM_PWM_ConfigChannel(&TIMER_InitStruct, &TIMER_OC_InitStruct, TIM_CHANNEL_3);
	  HAL_TIM_PWM_ConfigChannel(&TIMER_InitStruct, &TIMER_OC_InitStruct, TIM_CHANNEL_4);

	  HAL_TIM_PWM_Start(&TIMER_InitStruct,TIM_CHANNEL_3);
	  HAL_TIM_PWM_Start(&TIMER_InitStruct,TIM_CHANNEL_4);

	  s_motorRight.speed = 0;
	  s_motorLeft.speed = 0;

}


/**********************************************************
 * @brief  MotorRight_speed
 * @param  None
 * @retval speed
**********************************************************/
uint32_t MotorRight_speedRead()
{
  return(s_motorRight.speed);
}


/**********************************************************
 * @brief  MotorLeft_speed
 * @param  None
 * @retval speed
**********************************************************/
uint32_t MotorLeft_speedRead()
{
	return(s_motorLeft.speed);
}


/**********************************************************
 * @brief  MotorRight_speedWrite
 * @param  None
 * @retval speed
**********************************************************/
void MotorRight_speedWrite(uint32_t Motor_Speed)
{
  s_motorRight.speed = Motor_Speed;

  Motor_right(s_motorRight.direction, s_motorRight.speed);
}
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

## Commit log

2017-11-21 lib MRPiZ
    [BOM_Mechanic_MRPi1.ods]
2018-01-30 gerbers files
2018-01-31 STL files
    [PencilSupport.f3d, PencilSupport.stl, leftpincer.f3d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]
2018-02-26 Firmware STM32
2018-04-25 update firmware STM32
2018-11-04 feat: add camera and line follower example
2018-11-05 line_follower: handle keyboard interrupt.
2020-09-21 Update encoder.c
    Ajout du autoreload :
    TIM_AUTORELOAD_PRELOAD_DISABLE;
2020-10-14 Add files via upload
    Add rgb led control
